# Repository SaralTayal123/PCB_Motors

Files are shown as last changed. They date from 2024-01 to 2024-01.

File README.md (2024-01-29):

# PCB_Motors
Code &amp; Firmware to generate continuous coil PCB motor designs

Bare PCB Pictures: 
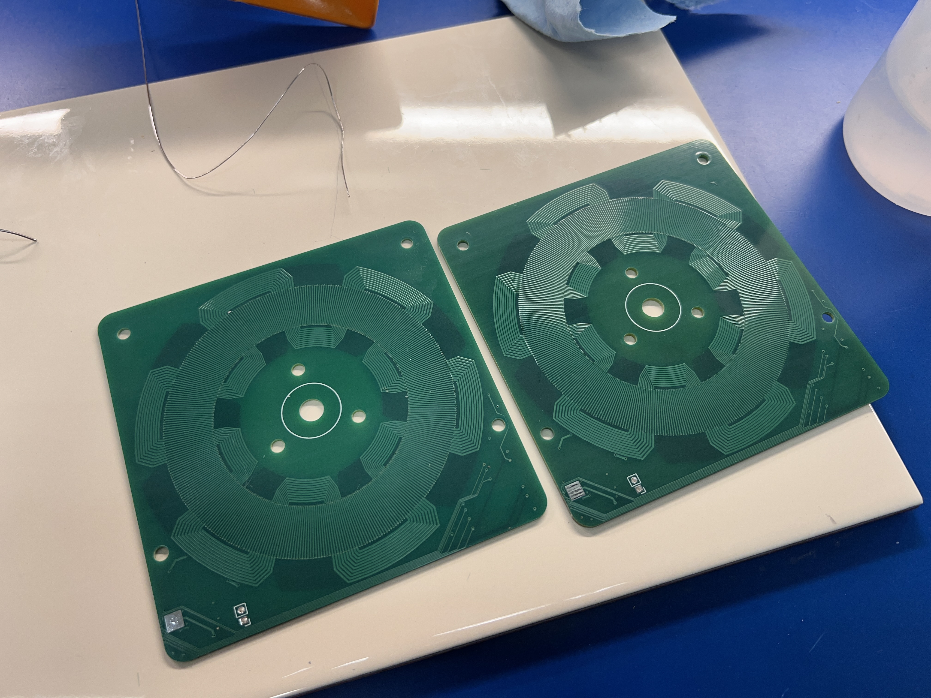
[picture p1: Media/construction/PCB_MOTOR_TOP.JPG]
PCB_MOTOR_TOP

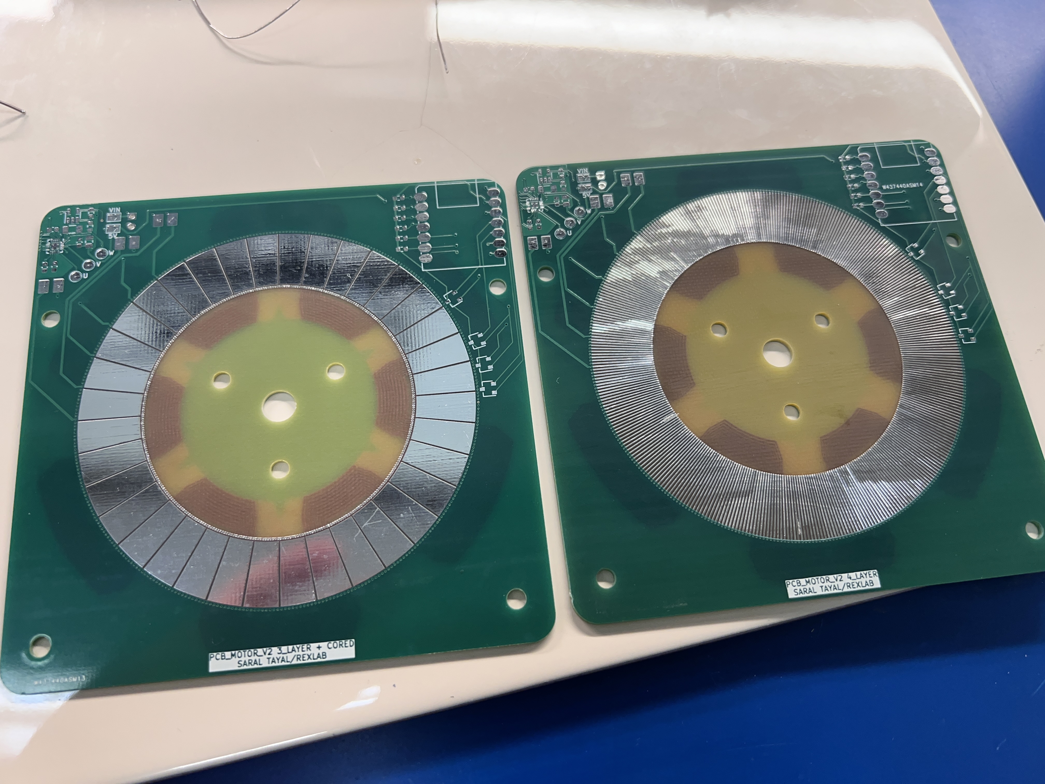
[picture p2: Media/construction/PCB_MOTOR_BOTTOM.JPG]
PCB_MOTOR_BOTTOM

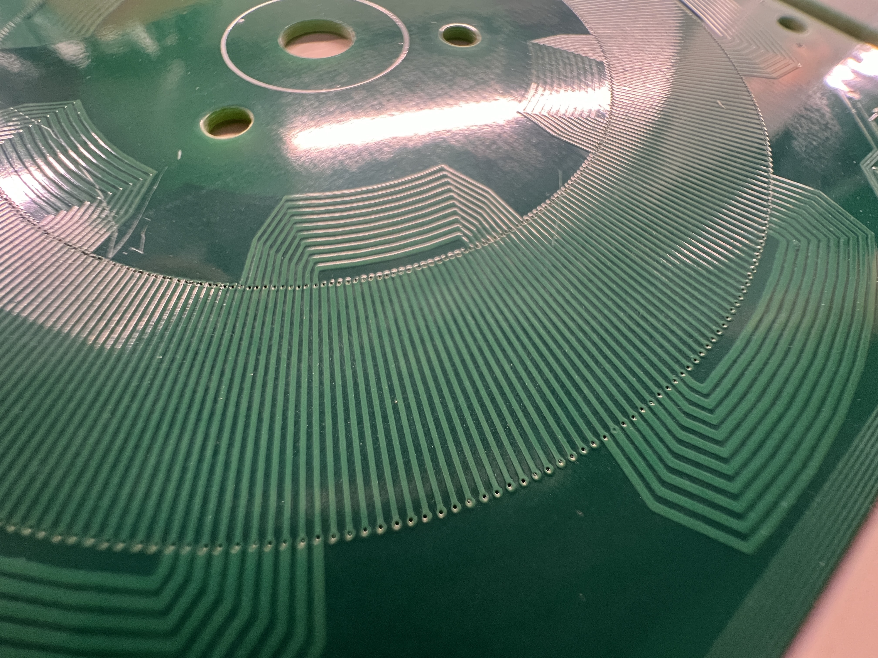
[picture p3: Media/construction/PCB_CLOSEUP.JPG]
PCB_CLOSEUP


Completed Dual PCB Stator, center rotor motor

PCB_Dual_T
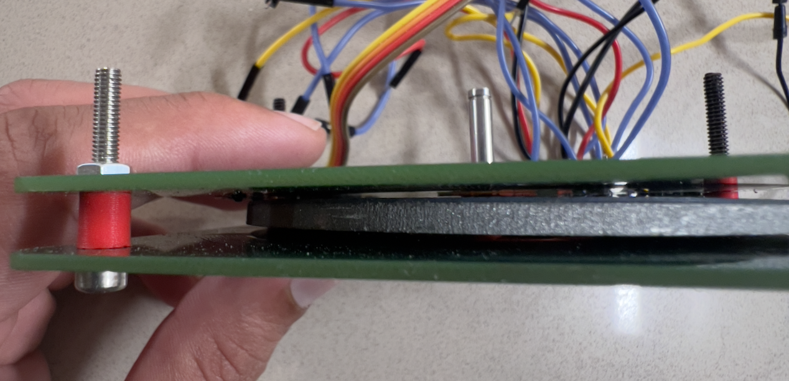
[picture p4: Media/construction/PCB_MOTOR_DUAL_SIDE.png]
PCB_Dual_S


## Media

Videos of the motor spinning and build pictures are in the Media folder

## Cloning the repo
Note that if you clone the repo, you will also need to intialize the submodules. You can do so as follows

```
git clone git@github.com:SaralTayal123/PCB_Motors.git
cd PCB_Motors

git submodule init
git submodule update
```

You will also need to delete/comment out line 6 of `kicad-coil-plugins/pcb_json.py` as follows

```
import json
import pandas as pd
import numpy as np
import matplotlib.pyplot as plt

# from helpers import rotate ### Modify by commenting out ###
```

## How to build your own motors

Option 1 *(Suggested)*: Simply use the existing kicad design and order the current designed version through a manufacturer like PCBway.

Option 2: Design your own PCB motors using the python script. Steps for that are outlined below

### Step 1: 
 
Calculate the appropriate winding pattern. Using the following link, find a slot-magnet combo that will produce a repeating pattern of "A", "B", "C". The ABC phases can be in any order and any case (upper or lower) as long as the pattern that they appear in are consistant. The other restriction is that your Slot number needs to be a multiple of 6 given this winding pattern. For example, I used a 36 slot, 12 magnet pole design and achieved a pattern of "AbC" as pictured below. The upper/lower case refers to the polarity of the coil phase and can be easily switched during wiring, which is why it's not case sensitive as long as the pattern is repeated. 

Calculator link: https://www.bavaria-direct.co.za/scheme/calculator/

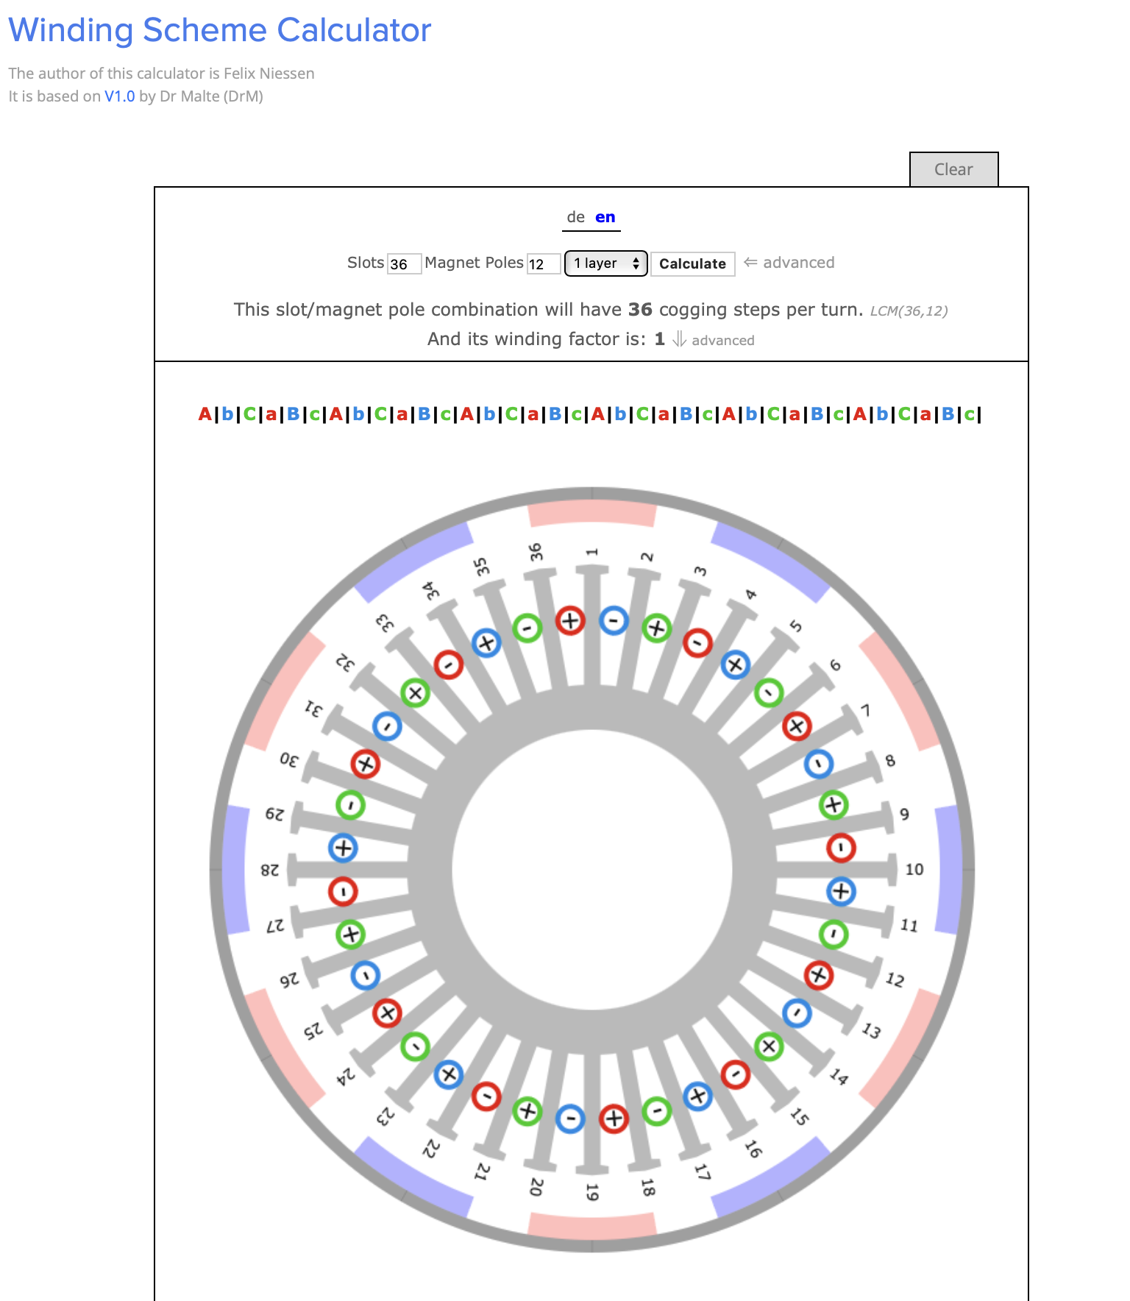
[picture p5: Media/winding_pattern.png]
winding_pattern


This step can be a little tedious since you will need to find magnets that will fit your motor inner/outer diameter while matching the pole pole pair count. If you need more flexibility on not requiring slots be a multiple of 6, or follow a different winding pattern, then this wave motor design isn't the best option for you, and a traditional repeated coil design like this is ideal for you: https://github.com/atomic14/kicad-coil-plugins/tree/216a77b6a4d9532b090e98a6620eb1c3f18db77d

### Step 2: Use the python script

Using the slot/pole combo from step 1 (or using the reccomended 36/12 design), open the continous_coil_gen.ipynb python notebook. Here, input the inner and outer diameter of your coils. You should tailor these to be the width of your magnets to make your motor as effective aas possible. You can also tune a few PCB trace parameters here depending on the capabilities of the PCB manufacturing available to you

### Step 3: Import the Kicad coil design into Kicad

Using the [tool here](https://github.com/atomic14/kicad-coil-plugins/tree/216a77b6a4d9532b090e98a6620eb1c3f18db77d), import your coil design into kicad. If you decide to work with my example board design in KiCad, you should right click the imported coil and move it to the origin to center it perfectly for your design.

Finally, integrate your coils with the rest of the motor controller circuitry to create your own PCB Motor!

## BOM for the example motor
Simple BOM, Cost is ~$25 + shipping
PCBWAY cost ~$26 for 5 boards + Shipping
Magnets 24 pieces @ $0.37 each = $30 (I recommend some spares as they tend to snap/break if they fly out of your hand into a metal object) : https://www.magnet4less.com/neodymium-bar-magnets-1-2-in-x-1-4-in-x-1-8-in-n42

### Rough Specs

Configuration: 2 sided PCB Stator, Rotor in the middle, 8V, Star wiring pattern

Stall torque: 0.008 Nm
Top Speed: 170 Rad/s
Max Power draw: 5 Watts
Peak output power (measured torque x angular velocity): 0.3 Watts

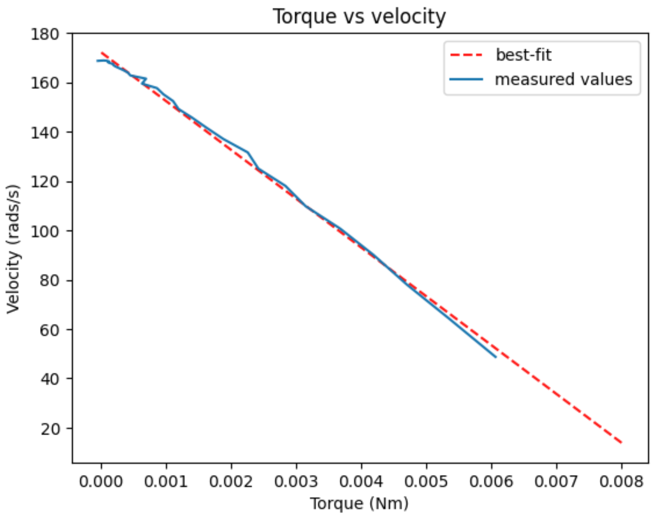
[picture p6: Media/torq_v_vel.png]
torq_v_vel

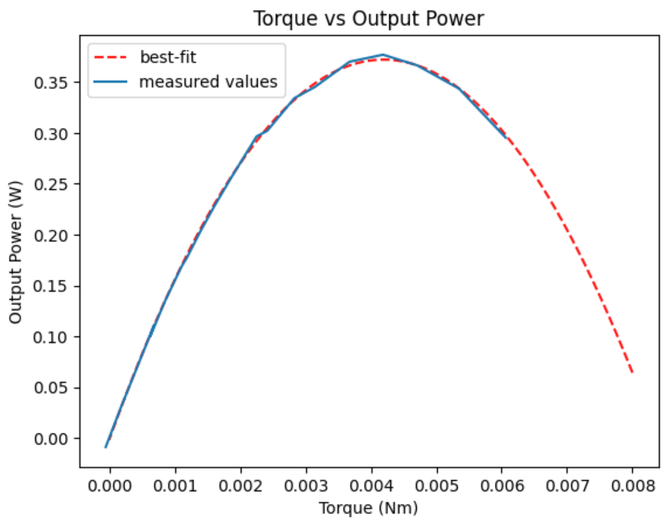
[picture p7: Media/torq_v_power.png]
torq_v_power


### Testing

Motor charecterization was performed by using 3d printed disc with bolts to serve as a known inertial load to our motor. Measuring the angular acceleration at a full torque command at each angular velocity allowed us to charecterize the torque curve of the motor and the output power curve for the motor (pictured above). This sort of testing is commonnly used for testing cars and is called an inertial dyno. The extra inertial load attached to the PCB motor is pictured below.

inertial_load

The neat thing about using this test is that all one needed to do was add some extra data-logging firmware, and the PCB motors can self-charecterize themselves without any external equipment!

We were also able to monitor a DC Amp-meter on the input power line of the motor to measure system efficiency, howerver there was a lot of switching noise on that power rail to measure a clean signal. Noisy graph is available in Media/torq_eff.png image. The efficiency test needs to be repeated with a low pass filter and a secondary means to test the motor with the motor controller out of the loop. 

### TODO: 
* Why this design
* Star vs Delta wiring
* How to pick winding factor and why conventional winding table won't work

Motor winding image credits: 
https://www.bavaria-direct.co.za/info/#prettyPhoto

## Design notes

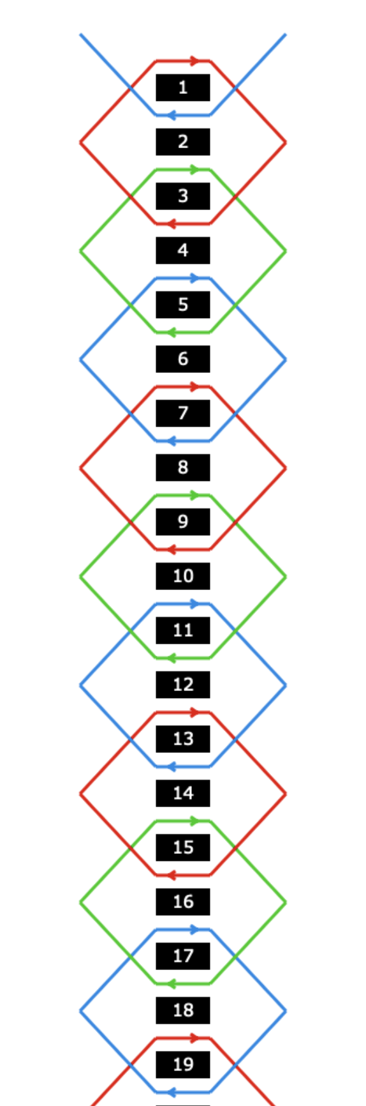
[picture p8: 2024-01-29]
Media/winding_pattern_2.png

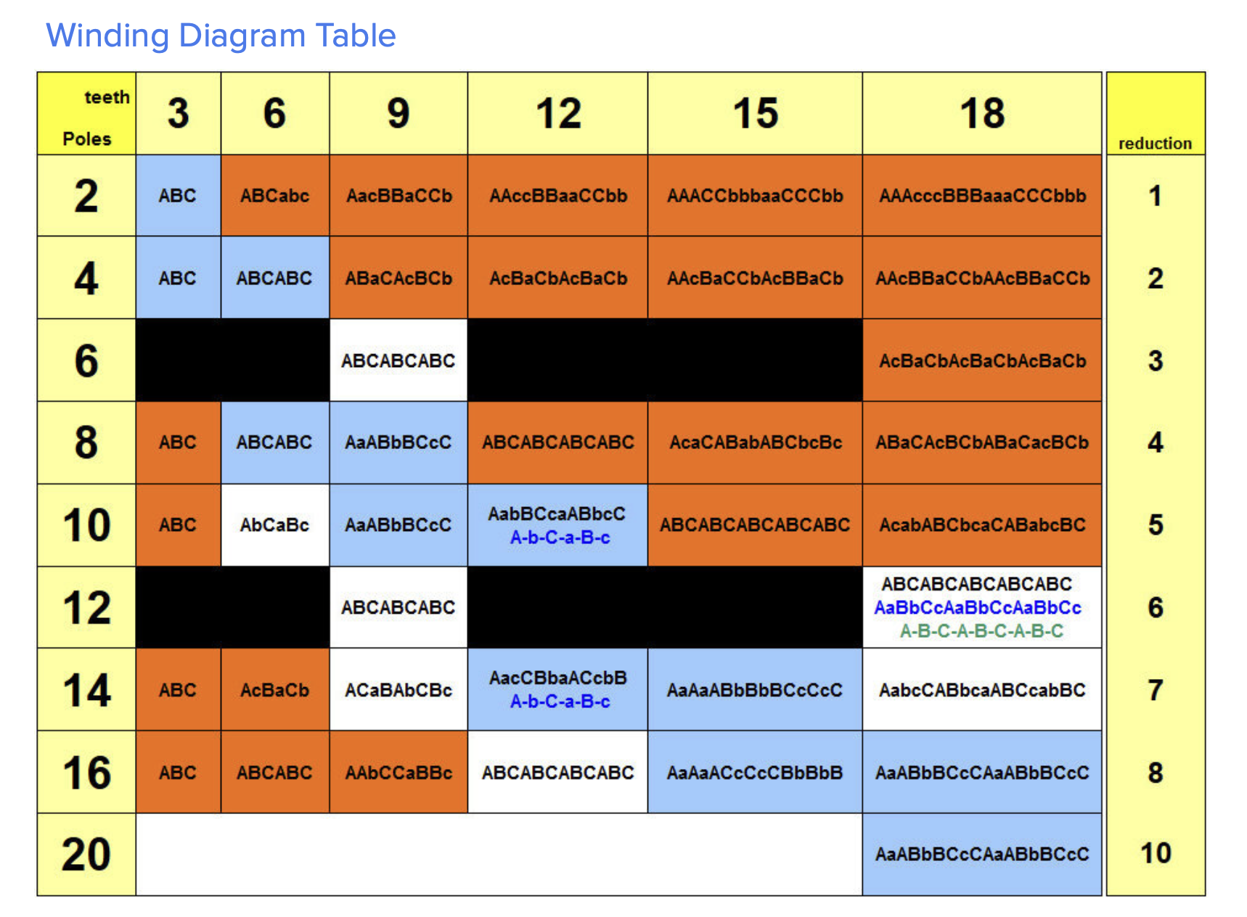
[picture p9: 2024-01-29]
Media/Screenshot 2024-01-18 at 6.25.13 PM.png

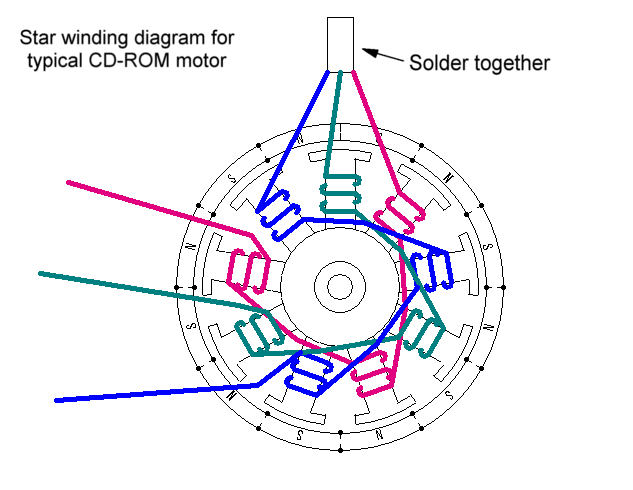
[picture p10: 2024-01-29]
Media/Wye_diagram.gif

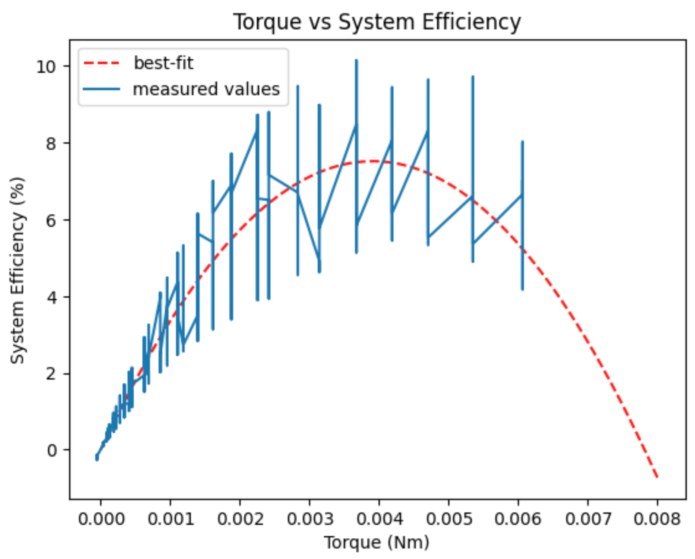
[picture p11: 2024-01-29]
Media/torq_eff.png

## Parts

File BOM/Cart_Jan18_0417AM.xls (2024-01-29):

SHOPPING CART
This is not an invoice
18-Jan-24 04:17:32
 | Mouser # | Mfr. # | Manufacturer | Customer # | Description | RoHS | Lifecycle | Order Qty. | Price (USD) | Ext.: (USD)
1 | 581-06035C104KAT2A | 06035C104KAT2A | KYOCERA AVX | C14, C15, C17, C21 | Multilayer Ceramic Capacitors MLCC - SMD/SMT NEW GLOBAL PN KGM15BR71H104KT 50V 0.1uF X7R 0603 10% | RoHS Compliant |  | 5 | $0.10 | $0.50
2 | 581-0805YC224MAT2A | 0805YC224MAT2A | KYOCERA AVX | C13 | Multilayer Ceramic Capacitors MLCC - SMD/SMT NEW GLOBAL PN KGM21AR71C224MU 16V .22uF X7R 0805 20% Tol | RoHS Compliant By Exemption |  | 2 | $0.23 | $0.46
3 | 603-RC0603FR-0710KL | RC0603FR-0710KL | YAGEO | R7, R8, R9, R10, R11 | Thick Film Resistors - SMD 10 kOhms 100mW 0603 1% | RoHS Compliant By Exemption |  | 5 | $0.10 | $0.50
4 | 71-WSL1206-0.1-E3 | WSL1206R1000FEB | Vishay | R1 | Current Sense Resistors - SMD 1/4watt .1ohms 1% | RoHS Compliant |  | 2 | $0.80 | $1.60
5 | 603-RC0603FR-072KL | RC0603FR-072KL | YAGEO | R2 | Thick Film Resistors - SMD 2 kOhms 100mW 0603 1% | RoHS Compliant By Exemption |  | 2 | $0.10 | $0.20
6 | 603-AC0603FR-1318KL | AC0603FR-1318KL | YAGEO | R3 | Thick Film Resistors - SMD 18 kOhms 100mW 0603 1% AEC-Q200 | RoHS Compliant By Exemption |  | 2 | $0.12 | $0.24
7 | 595-DRV5011ADDBZR | DRV5011ADDBZR | Texas Instruments | U3, U4, U6 | Board Mount Hall Effect / Magnetic Sensors Small size (available in WCSP and X2SON), low voltage (up to 5.5-V) Hall effect latch 3-SOT-23 -40 to 135 | RoHS Compliant |  | 4 | $0.44 | $1.76
8 | 785-SS360ST | SS360ST | Honeywell | U3, U4, U6 | Board Mount Hall Effect / Magnetic Sensors SOT-23 Bipolar Latch South Pole Activate | RoHS Compliant |  | 4 | $0.89 | $3.56
9 | 700-TMC6300-LA | TMC6300-LA | Analog Devices Inc. | U3 | Motor / Motion / Ignition Controllers & Drivers Highly Efficient Low Voltage, Zero Standby Current Driver for 3-Phase BLDC/PMSM Motors up to 2A peak, Triple Half-Bridge with separate HS and LS control signals | RoHS Compliant |  | 1 | $2.75 | $2.75
10 | 713-113991114 | 113991114 | Seeed Studio | U1 | Multiprotocol Modules XIAO ESP32S3 - 2.4GHz WiFi, BLE 5.0, Dual-Core, Battery Charge,Smart Homes, IoT, Wearable Devices, Robotics |  | New Product | 1 | $7.49 | $7.49
11 | 595-LM321LVIDBVR | LM321LVIDBVR | Texas Instruments | U2 | Operational Amplifiers - Op Amps Single, 5.5-V, 1-MHz, 3-mV offset voltage operational amplifier 5-SOT-23 -40 to 125 | RoHS Compliant |  | 1 | $0.24 | $0.24
12 | 700-MAX17502EATB+T | MAX17502EATB+T | Analog Devices Inc. |  | Switching Voltage Regulators 60V, 1A, Ultra-Small, High-Efficiency, Synchronous Step-Down DC-DC Converter | RoHS Compliant |  | 1 | $5.33 | $5.33
By submitting your order you agree to these terms and conditions. (https://www.mouser.com/saleterms) |  |  |  |  |  |  |  |  | Merchandise: | $24.63
Prices are reflected at the date and time shown. |  |  |  |  |  |  |  |  | Shipping Charge: | $7.99

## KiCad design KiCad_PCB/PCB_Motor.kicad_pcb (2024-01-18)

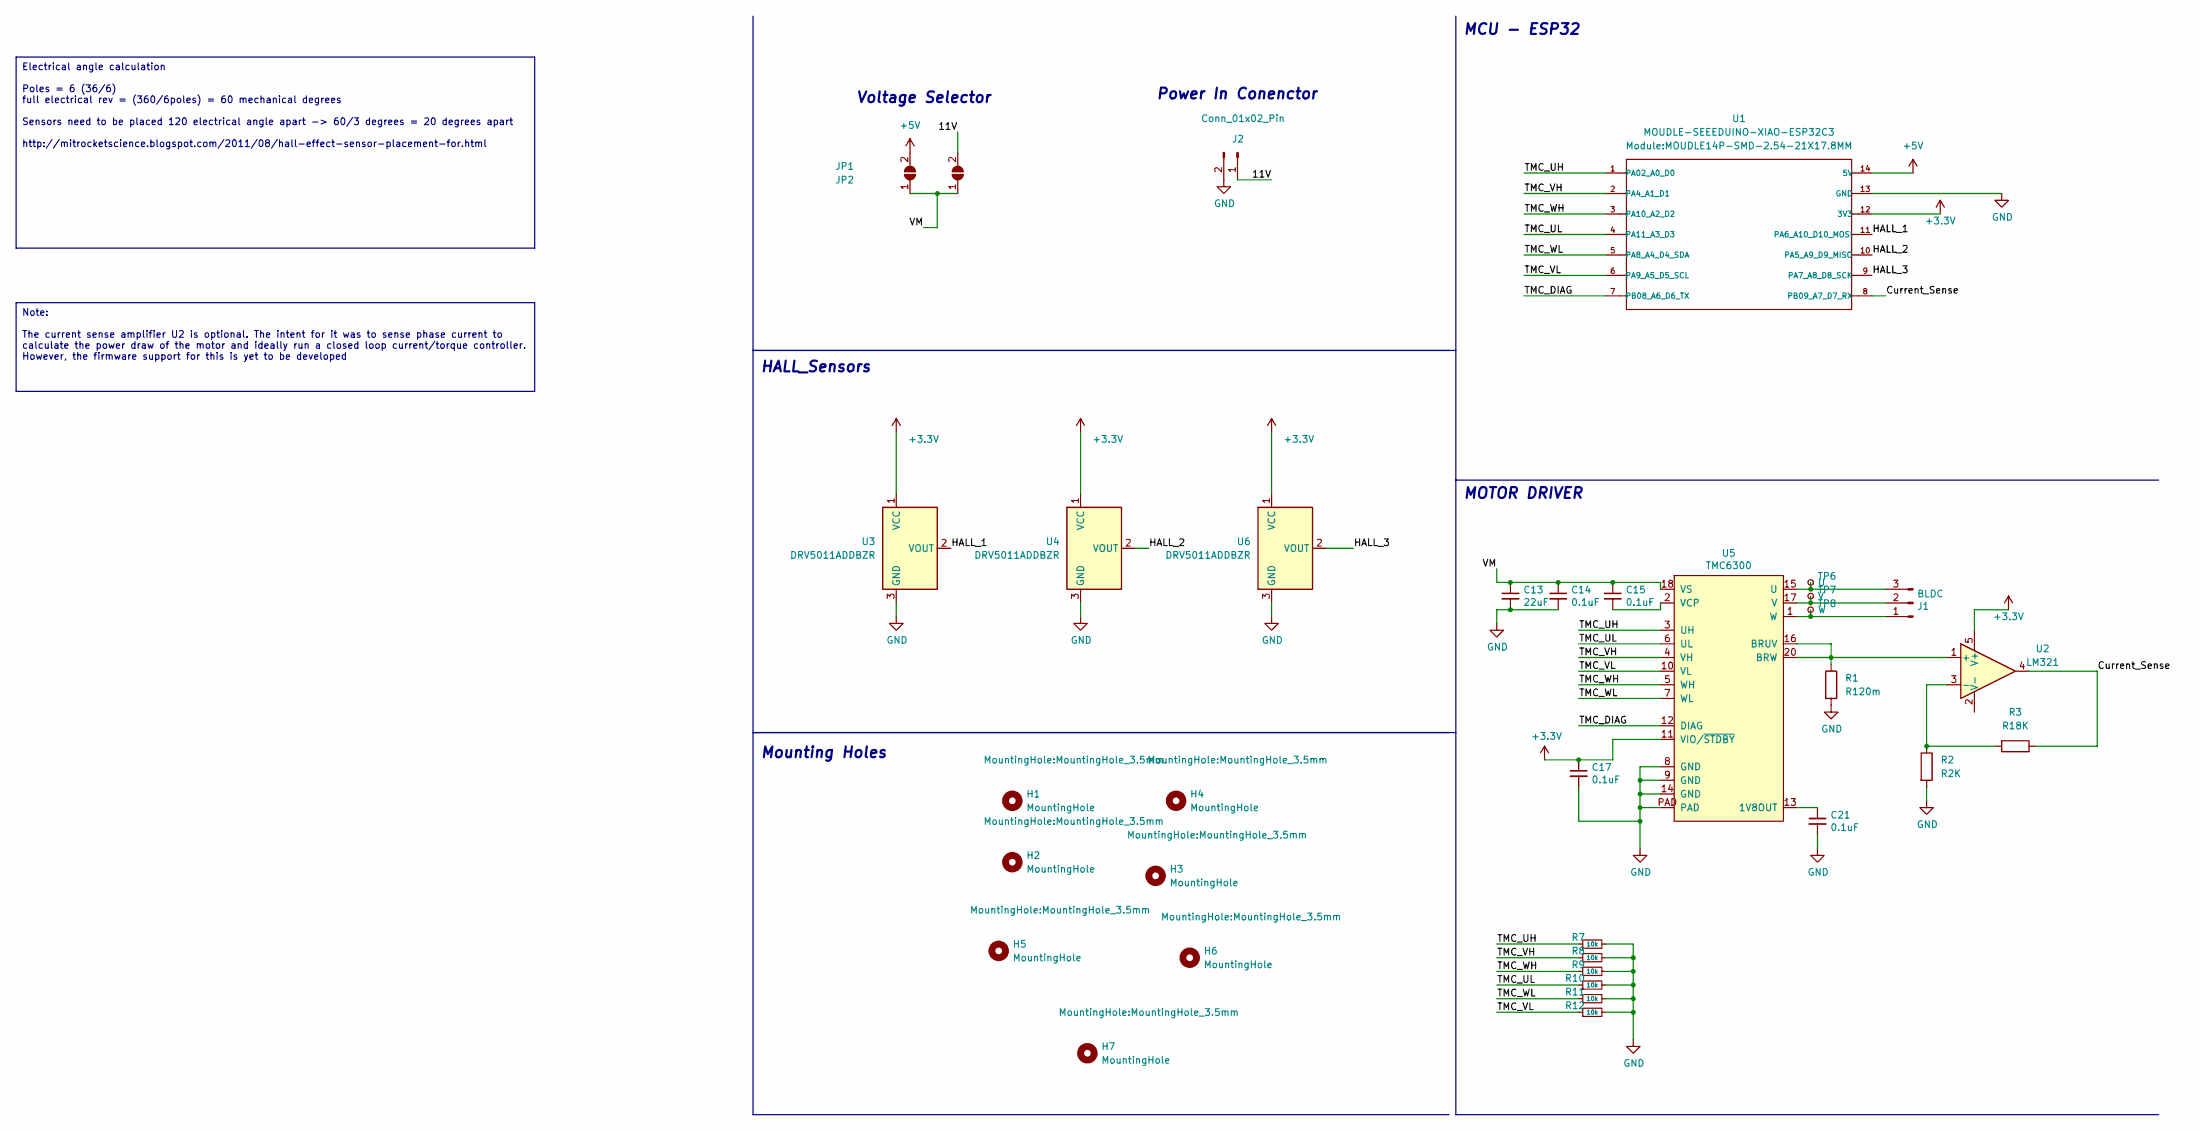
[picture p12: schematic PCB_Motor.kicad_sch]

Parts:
C13: 22uF; C_0805_2012Metric; LCSC C98190
C14, C15, C17, C21: 0.1uF; C_0603_1608Metric; LCSC C1591
H1, H2, H3, H4, H5, H6, H7: MountingHole; MountingHole_3.5mm
J1: BLDC; 532610371; LCSC C293630
J2: Conn_01x02_Pin; PinHeader_1x02_P2.54mm_Vertical
JP1, JP2: SolderJumper_2_Open; SolderJumper-2_P1.3mm_Open_TrianglePad1.0x1.5mm
R1: R120m; R_1206_3216Metric
R2: R2K; R_0603_1608Metric
R3: R18K; R_0603_1608Metric
R7, R8, R9, R10, R11, R12: 10k; R_0603_1608Metric; LCSC C98220
TP6: U; TestPoint_Pad_D2.0mm_ValueSilk
TP7: V; TestPoint_Pad_D2.0mm_ValueSilk
TP8: W; TestPoint_Pad_D2.0mm_ValueSilk
U1: MOUDLE-SEEEDUINO-XIAO-ESP32C3; MOUDLE14P-SMD-2.54-21X17.8MM
U2: LM321; SOT-23-5
U3, U4, U6: DRV5011ADDBZR; SOT-23W
U5: TMC6300; QFN-20-1EP_3x3mm_P0.4mm_EP1.65x1.65mm_ThermalVias_LargerVia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; Digikey TMC6300-LA-T

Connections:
+3V3: C17.1, U1.12 (3V3), U2.5 (V+), U3.1 (VCC), U4.1 (VCC), U5.11 (VIO/~STDBY), U6.1 (VCC)
+5V: JP1.2 (B), U1.14 (5V)
/11V: J2.1, JP2.2 (B)
/Current_Sense: R3.2, U1.8 (PB09_A7_D7_RX), U2.4
/HALL_1: U1.11 (PA6_A10_D10_MOSI), U3.2 (VOUT)
/HALL_2: U1.10 (PA5_A9_D9_MISO), U4.2 (VOUT)
/HALL_3: U1.9 (PA7_A8_D8_SCK), U6.2 (VOUT)
/TMC_DIAG: U1.7 (PB08_A6_D6_TX), U5.12 (DIAG)
/TMC_UH: R7.1, U1.1 (PA02_A0_D0), U5.3 (UH)
/TMC_UL: R10.1, U1.4 (PA11_A3_D3), U5.6 (UL)
/TMC_VH: R8.1, U1.2 (PA4_A1_D1), U5.4 (VH)
/TMC_VL: R12.1, U1.6 (PA9_A5_D5_SCL), U5.10 (VL)
/TMC_WH: R9.1, U1.3 (PA10_A2_D2), U5.5 (WH)
/TMC_WL: R11.1, U1.5 (PA8_A4_D4_SDA), U5.7 (WL)
/VM: C13.1, C14.1, C15.1, JP1.1 (A), JP2.1 (A), U5.18 (VS)
GND: C13.2, C14.2, C17.2, C21.2, J2.2, R1.2, R2.2, R7.2, R8.2, R9.2, R10.2, R11.2, R12.2, U1.13 (GND), U3.3 (GND), U4.3 (GND), U5.8 (GND), U5.9 (GND), U5.14 (GND), U5.PAD, U6.3 (GND)
unnamed: J1.1, TP8.1, U5.1 (W)
unnamed: J1.2, TP7.1, U5.17 (V)
unnamed: J1.3, TP6.1, U5.15 (U)
unnamed: R1.1, U2.1 (+), U5.16 (BRUV), U5.20 (BRW)
unnamed: R2.1, R3.1, U2.3 (-)
unnamed: C21.1, U5.13 (1V8OUT)
unnamed: C15.2, U5.2 (VCP)

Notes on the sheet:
Note: The current sense amplifier U2 is optional. The intent for it was to sense phase current to calculate the power draw of the motor and ideally run a closed loop current/torque controller. However, the firmware support for this is yet to be developed
Electrical angle calculation Poles = 6 (36/6) full electrical rev = (360/6poles) = 60 mechanical degrees Sensors need to be placed 120 electrical angle apart -> 60/3 degrees = 20 degrees apart http://mitrocketscience.blogspot.com/2011/08/hall-effect-sensor-placement-for.html
Power In Conenctor
MCU - ESP32
MOTOR DRIVER
Voltage Selector
HALL_Sensors
Mounting Holes

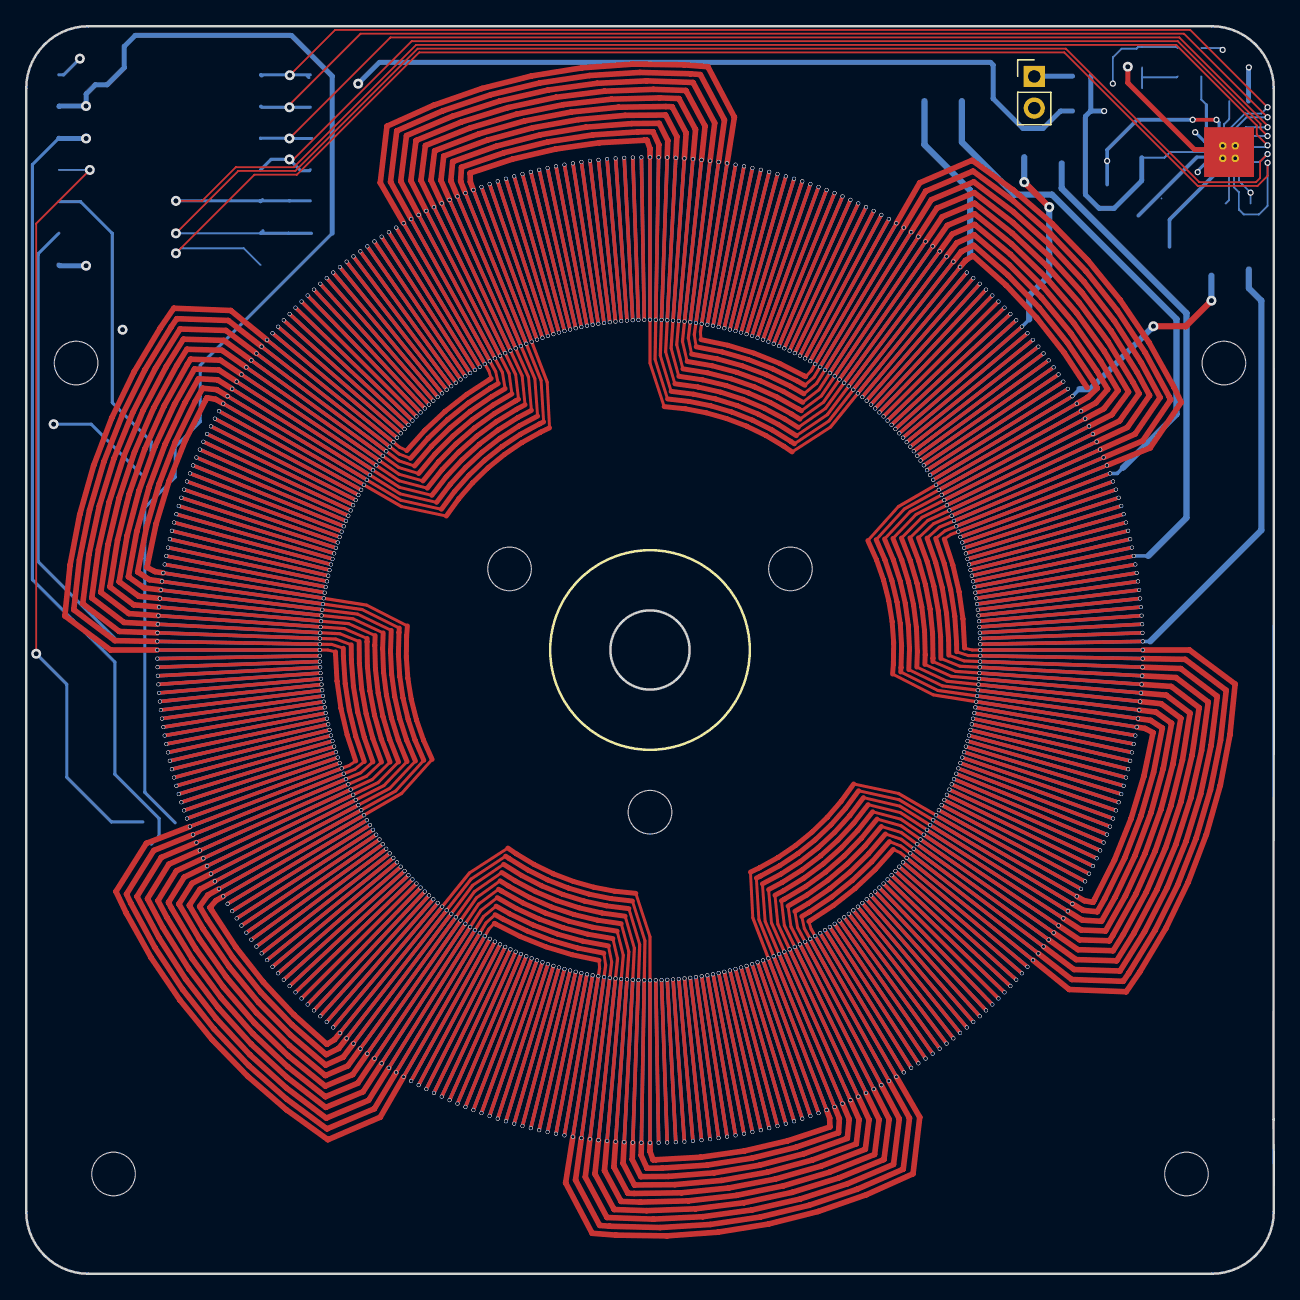
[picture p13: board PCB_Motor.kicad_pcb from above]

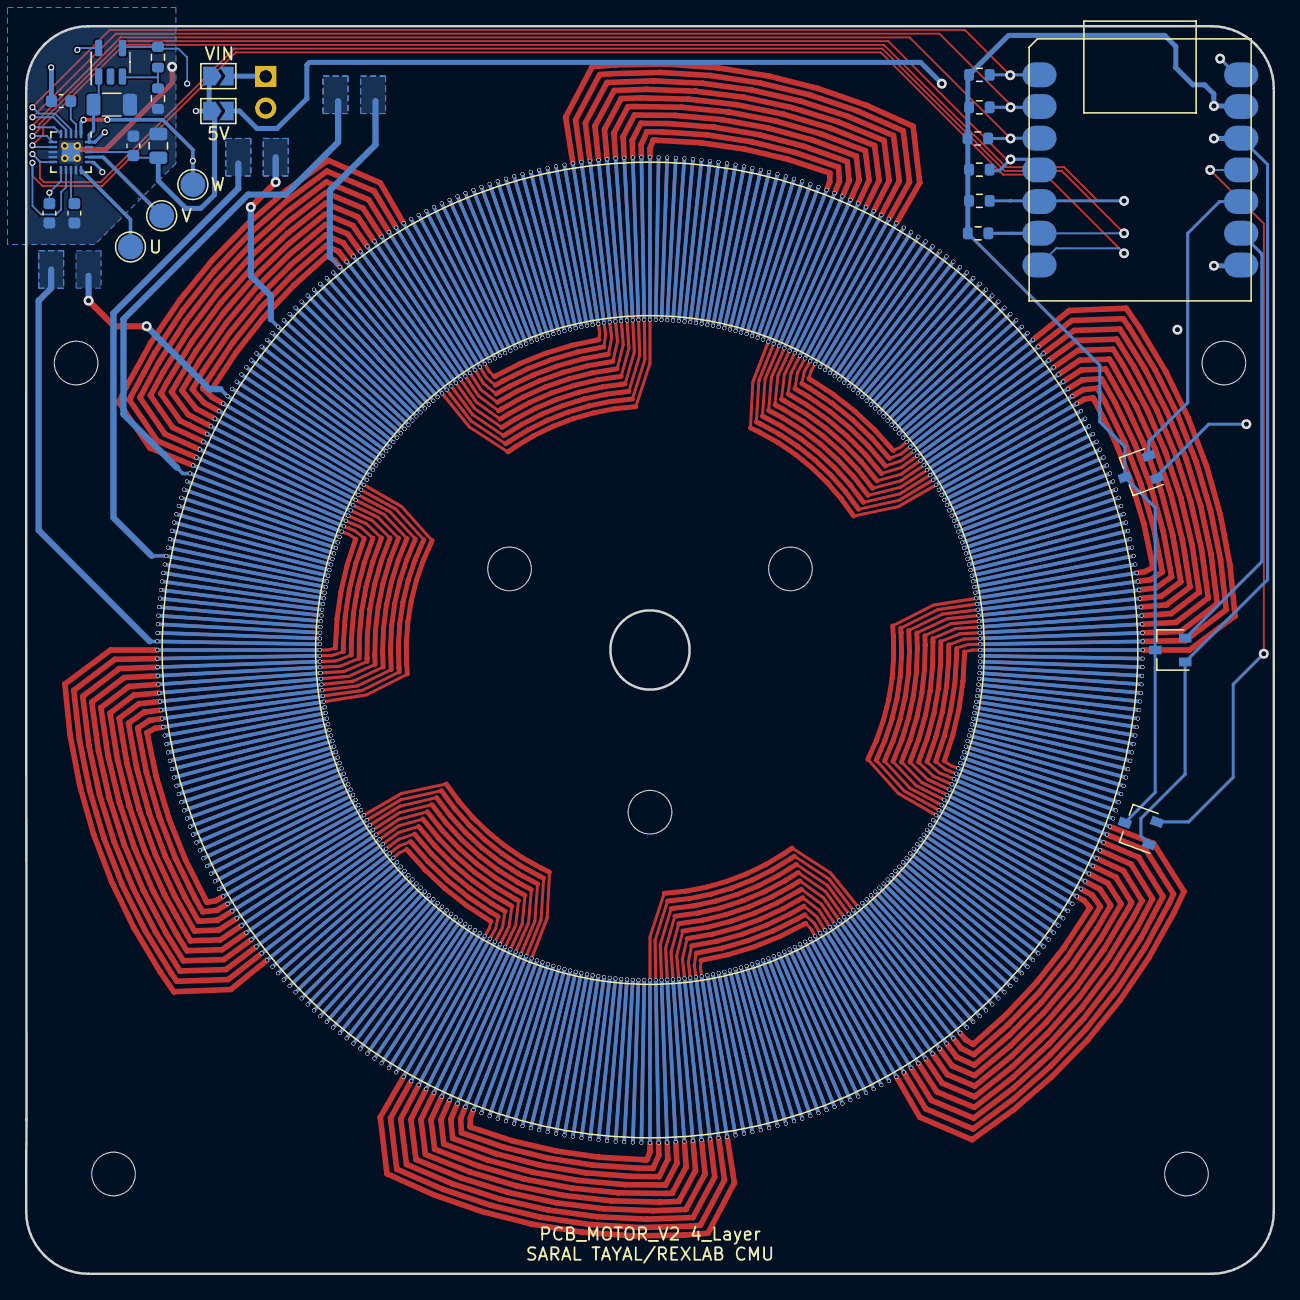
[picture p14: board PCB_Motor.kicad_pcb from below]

Board: 4 copper layers, 100.0 x 100.0 mm, 33 parts (25 on the bottom side), 23 nets.

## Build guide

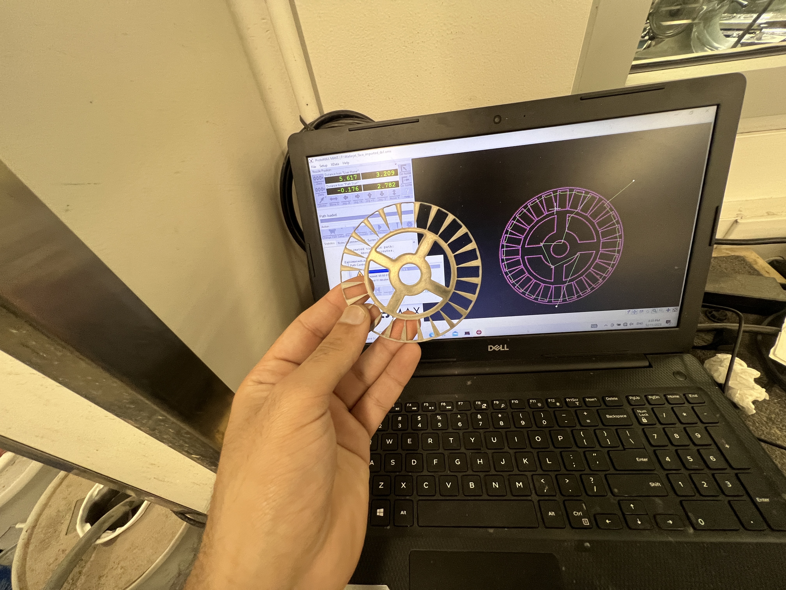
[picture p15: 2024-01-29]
Media/construction/IMG_8790.JPG

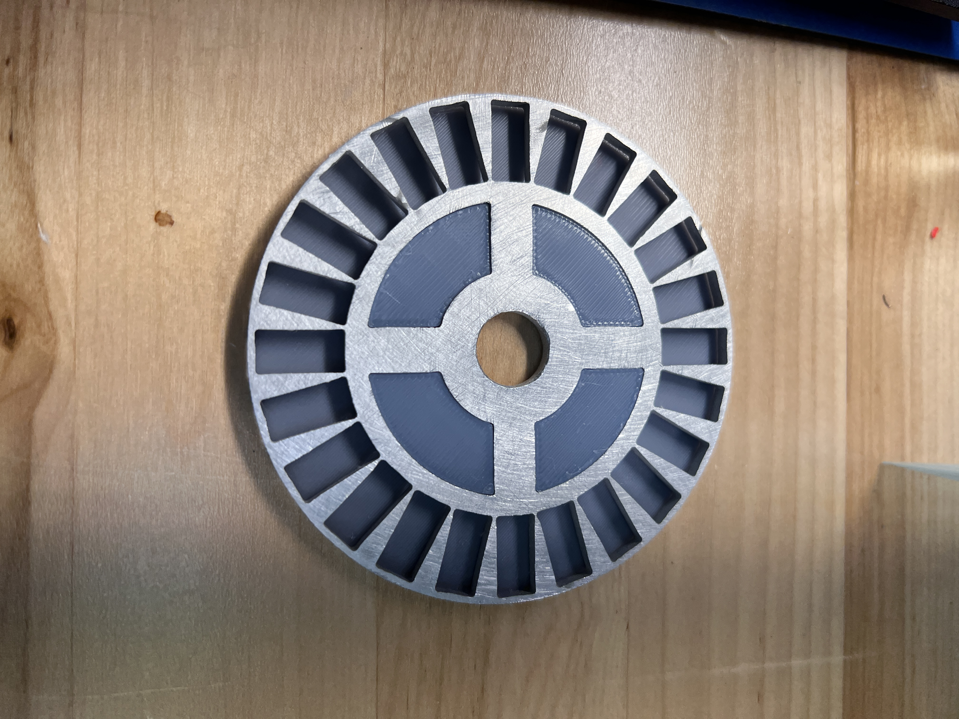
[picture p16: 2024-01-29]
Media/construction/IMG_8796.JPG

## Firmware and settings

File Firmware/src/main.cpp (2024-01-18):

#include <SimpleFOC.h>
#include <Wire.h>

#define PIN_UH 1
#define PIN_UL 4
#define PIN_VH 2
#define PIN_VL 5
#define PIN_WH 3
#define PIN_WL 6

#define PP 6
// BLDC motor & driver instance
static BLDCMotor motor = BLDCMotor(PP, 6);
BLDCDriver6PWM driver = BLDCDriver6PWM(PIN_UH, PIN_UL, PIN_VH, PIN_VL, PIN_WH, PIN_WL);

// hall sensors
#define HALL_A 7
#define HALL_B 8
#define HALL_C 9
HallSensor sensor = HallSensor(HALL_A, HALL_B, HALL_C, PP);
void doA(){sensor.handleA();}
void doB(){sensor.handleB();}
void doC(){sensor.handleC();}

// instantiate the commander
Commander command = Commander(Serial);
void doTarget(char* cmd) { command.scalar(&motor.target, cmd); }
void PID (char* cmd) { command.pid(&motor.PID_velocity, cmd); }
// GenericSensor sensor = GenericSensor(get_mag_sensor_angle, init_magnetic_sensor);

void setup() { 
  Wire.begin(43, 44);

  Serial.begin(115200);
  delay(2000);
  Serial.println("init");

  sensor.init();

  sensor.init();
  sensor.enableInterrupts(doA, doB, doC);


  // link the motor to the sensor
  motor.linkSensor(&sensor);
  // motor.LPF_velocity.Tf = 0.98;
  motor.LPF_velocity.Tf = 0.5;


  // driver config
  // power supply voltage [V]
  driver.voltage_power_supply = 11;
  Serial.println("driver init");
  driver.init();
  // link driver
  motor.linkDriver(&driver);

  // aligning voltage
  motor.voltage_sensor_align = 4;

  // set a max limit for the motor
  motor.voltage_limit = 7; // [V]
  motor.current_limit = 7;

  motor.sensor_direction = CCW;

  // set motion control loop to be used
  // motor.torque_controller = TorqueControlType::voltage;
  // motor.controller = MotionControlType::torque;
  motor.controller = MotionControlType::velocity;

  motor.PID_velocity.P = 0.45;
  motor.PID_velocity.I = 0.01;
  motor.PID_velocity.D = 0.3;

  // motor.controller = MotionControlType::velocity_openloop;

  motor.useMonitoring(Serial);

  // initialize motor
  motor.init();
  // align sensor and start FOC
  motor.initFOC();

  // set the initial motor target
  motor.target = 0; // Volts 

  // add target command T
  // command.add('T', doTarget, "target current"); // - if phase resistance defined
  command.add('T', doTarget, "target voltage");
  command.add('C', PID, "PID velocity");

  Serial.println(F("Motor ready."));
  Serial.println(F("Set the target using serial terminal:"));
  _delay(1000);

}

static int counter = 0;
void loop() {
  // main FOC algorithm function
  motor.loopFOC();

  // Motion control function
  motor.move();

  // Serial.println(encoder.getAngle());

  // // user communication
  command.run();
}

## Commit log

2024-01-17 inital sync commit
    [PCB_Motor.kicad_pcb]
2024-01-18 Sync firmware and PCB
    [PCB_Motor.kicad_pcb, PCB_Motor.kicad_sch]
2024-01-29 Updated docs
    Media doc
    shrunk video file size
    [Cart_Jan18_0417AM.xls]
